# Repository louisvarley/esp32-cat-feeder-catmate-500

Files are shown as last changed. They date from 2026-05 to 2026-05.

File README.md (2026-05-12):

# ESP32 Cat Feeder (Cat Mate 500 + Home Assistant)

This project started for one simple reason: I needed to feed my cat properly when I was away. she only eats very small meals multiple times a day. 

The **Cat Mate C500** is great feeder, but it is built around a short timer cycle if only 24 hours. I wanted something I could control remotely and schedule flexibly with **Home Assistant**, including windows longer than 24 hours.

With two C500 units and ice packs, I can keep 8 small meals fresh for around **48 hours**. That gives me a much better safety margin for overnight trips and weekends for work. I prefer being able to watch on camera and judge when she needs feeding rather than 
merely a timer.

# ESP32-C3 Cat Feeder

A hacked C500 cat feeder controlled via a web interface and Home Assistant, built around an ESP32-C3 board with built-in OLED.

---

## Components

| Component | Value / Part | Purpose |
|---|---|---|
| ESP32-C3 with OLED | Diymore ESP32-C3 | Main controller, web server, display |
| IR Optical Sensor | ITR9608 | Detects bowl position, has one already but this is more reliable and is 3.3v compatable.. ok i might have blown up the originals... |
| NPN Transistor | 2N2222A | Motor switching |
| Flyback Diode | 1N4007 | Motor spike protection |
| Resistor | 1kΩ  | Transistor base current limiting |
| Resistor | 200Ω | IR LED current limiting |
| USB-C Breakout Board | With CC1/CC2 pins | Power input for mounting the power elsewhere |

---

## Wiring

### Power
```
USB 5V              →  V5 pin on ESP32
USB GND             →  GND pin on ESP32
CC1 on breakout     →  5.1kΩ  →  GND  (if not already on breakout board)
CC2 on breakout     →  5.1kΩ  →  GND  (if not already on breakout board)
```

### Motor Circuit
```
V3 (3.3V)           →  Motor +
Motor -             →  2N2222A Collector (middle leg, flat face forward)
2N2222A Emitter     →  GND              (left leg, flat face forward)
GPIO 3              →  1kΩ  →  2N2222A Base  (right leg, flat face forward)

Flyback diode across motor terminals:
  Stripe (cathode)  →  Motor + (3.3V side)
  No stripe (anode) →  Motor - (Collector side)
```

### IR Sensor (ITR9608)
```
Pin 1 (Anode)       →  200Ω  →  3.3V   (emitter/LED side)
Pin 2 (Cathode)     →  GND              (emitter/LED side)
Pin 3 (Collector)   →  GPIO 4           (receiver/output side)
Pin 4 (Emitter)     →  GND              (receiver/output side)
```

> Note: GPIO 4 uses INPUT_PULLUP in code — no external pull up resistor needed.

### OLED Display
```
Internal to board — no wiring needed
SDA  →  GPIO 5 (internal)
SCL  →  GPIO 6 (internal)
```

### Boot Button
```
Internal to board — no wiring needed
GPIO 9 (internal)
```

---

## GPIO Summary

| GPIO | Function |
|---|---|
| GPIO 3 | Motor control (via 2N2222A) |
| GPIO 4 | IR sensor signal |
| GPIO 5 | OLED SDA (internal) |
| GPIO 6 | OLED SCL (internal) |
| GPIO 9 | Boot button (internal) |

---

## Libraries Required

Install via Arduino IDE Library Manager:

- **U8g2** by oliver
- **WiFiManager** by tzapu

---

## Usage

### First Boot
1. Power on the device
2. Connect to the **CATFEEDER###** WiFi network (no password)
3. Open browser to **192.168.4.1**
4. Enter your WiFi details and select DHCP or Static IP
5. Device restarts and connects

### Web Interface
Navigate to the device IP address in any browser to access the feed button.

### Manual Feed
Press the boot button once to trigger a feed.

### Reset WiFi
Hold the boot button for 10 seconds — device clears WiFi settings and restarts into AP mode.

### Home Assistant
Add to `configuration.yaml`:
```yaml
rest_command:
  cat_feeder_1:
    url: "http://<device-ip>/feed"
    method: GET
```

Then call `rest_command.cat_feeder_1` from automations or the dashboard.

---

## Notes

- Motor runs on 3.3V — original feeder ran on 2-3x AA batteries so 3.3V is fine
- IR sensor requires 200Ω current limiting resistor on LED side — without it the LED will burn out
- WiFi TX power is reduced to `WIFI_POWER_8_5dBm` to fix cold boot connection issues on this board
- USB-C breakout board must have CC1 and CC2 pulled to GND via 5.1kΩ resistors to negotiate power from charger

## Libraries used

- `WiFi.h`
- `WebServer.h`
- `WiFiManager.h`
- `Preferences.h`
- `Wire.h`
- `U8g2lib.h`

Install these in Arduino IDE before compiling.

## Upload and run

1. Open `cat_feeder/cat_feeder.ino` in Arduino IDE.
2. Install required libraries.
3. Select your ESP32 board + COM port.
4. Upload firmware.
5. On first boot, connect to AP shown on OLED (`CATFEEDERxxx`) and set Wi-Fi.
6. Open the ESP32 IP address in browser or call `/feed` from Home Assistant.

## 3d Prints

Included 3 STL's for mounting the board in the space the existing LCD goes and for mounting external USB C breakout board with a little super glue! 

Enjoy! Spend time with your cat and don't let the robots do all the feeding!

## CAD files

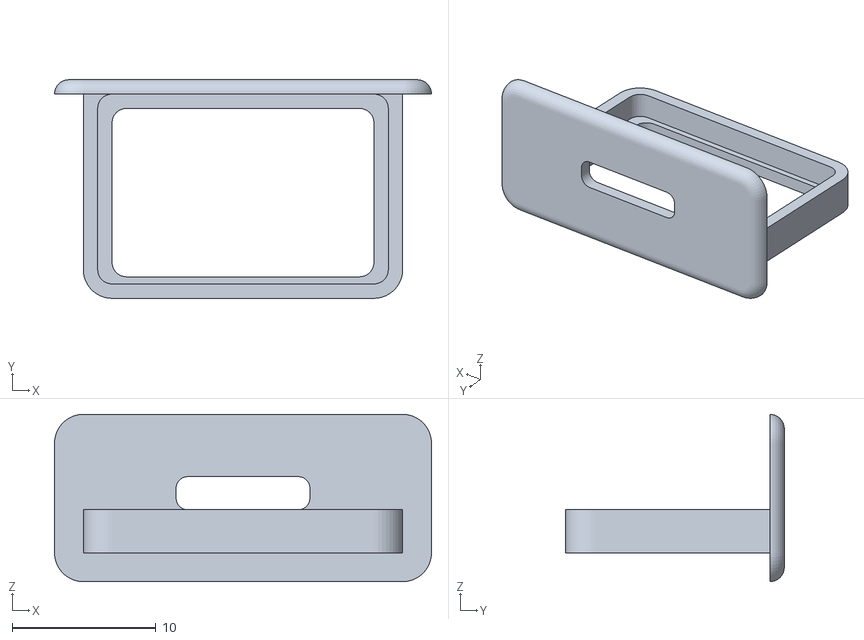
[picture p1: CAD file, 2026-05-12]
USB Socket.stl
26.2 x 15.2 x 11.6

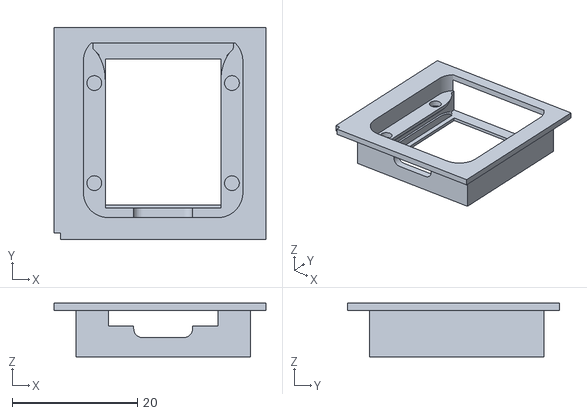
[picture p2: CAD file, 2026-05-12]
Holder.stl
33.9 x 33.9 x 8.62

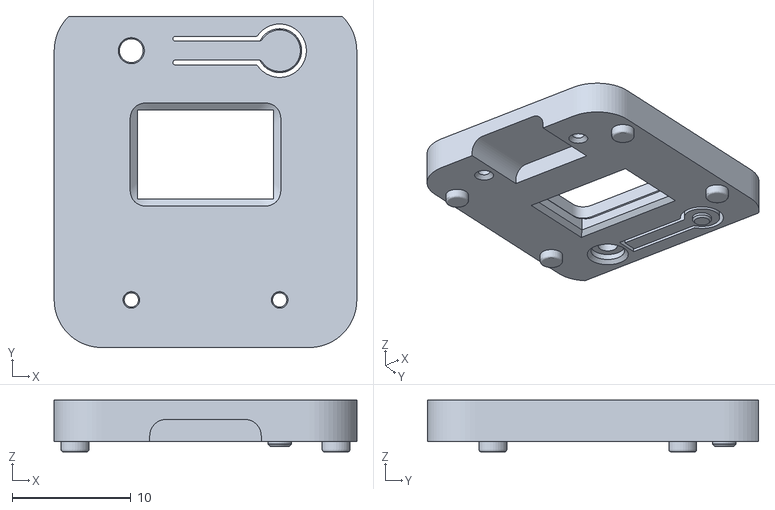
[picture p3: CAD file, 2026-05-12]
Cap.stl
25.5 x 27.9 x 4.38

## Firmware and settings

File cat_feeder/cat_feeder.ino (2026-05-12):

#include <WiFi.h>
#include <WebServer.h>
#include <WiFiManager.h>
#include <Preferences.h>
#include <Wire.h>
#include <U8g2lib.h>

#define MOTOR_PIN 3
#define SENSOR_PIN 4
#define BOOT_BUTTON 9
#define SDA_PIN 5
#define SCL_PIN 6

U8G2_SSD1306_72X40_ER_F_HW_I2C display(U8G2_R0, U8X8_PIN_NONE, SCL_PIN, SDA_PIN);
WebServer server(80);
Preferences preferences;

String lastFed = "Never";
bool feeding = false;

void updateOLED(String line1, String line2) {
  display.clearBuffer();
  display.setFont(u8g2_font_6x10_tr);
  display.drawStr(0, 12, line1.c_str());
  display.drawStr(0, 28, line2.c_str());
  display.sendBuffer();
}

void feed() {
  if (feeding) return;
  feeding = true;
  Serial.println("Feeding...");
  updateOLED("Feeding...", "");
  digitalWrite(MOTOR_PIN, HIGH);
  delay(200);
  unsigned long timeout = millis() + 5000;
  while (digitalRead(SENSOR_PIN) == HIGH) {
    if (millis() > timeout) {
      Serial.println("Timeout!");
      break;
    }
  }
  digitalWrite(MOTOR_PIN, LOW);
  lastFed = String(millis() / 60000) + "min ago";
  Serial.println("Fed!");
  updateOLED("Fed!", lastFed);
  delay(2000);
  feeding = false;
}

void handleRoot() {
  String html = "";
  html += "<!DOCTYPE html><html><head>";
  html += "<meta name='viewport' content='width=device-width, initial-scale=1'>";
  html += "<title>Cat Feeder</title>";
  html += "<style>";
  html += "body{font-family:sans-serif;display:flex;flex-direction:column;align-items:center;justify-content:center;min-height:100vh;margin:0;background:#1a1a2e;color:white;}";
  html += "h1{font-size:2em;margin-bottom:0.2em;}";
  html += "p{color:#aaa;margin-bottom:2em;}";
  html += "button{background:#e94560;color:white;border:none;padding:20px 50px;font-size:1.5em;border-radius:12px;cursor:pointer;}";
  html += "button:active{background:#c73652;}";
  html += ".last{margin-top:2em;color:#aaa;font-size:0.9em;}";
  html += "</style></head><body>";
  html += "<h1>Cat Feeder</h1>";
  html += "<p>Press to dispense one portion</p>";
  html += "<button onclick=\"fetch('/feed').then(function(){document.querySelector('.last').innerText='Feeding...';setTimeout(function(){location.reload();},3000);})\">Feed Now</button>";
  html += "<div class='last'>Last fed: " + lastFed + "</div>";
  html += "</body></html>";
  server.send(200, "text/html", html);
}

void handleFeed() {
  feed();
  server.send(200, "text/plain", "OK");
}

void setup() {
  Serial.begin(115200);
  delay(6000);  // wait for everything to stabilise on cold boot

  pinMode(MOTOR_PIN, OUTPUT);
  pinMode(SENSOR_PIN, INPUT_PULLUP);
  pinMode(BOOT_BUTTON, INPUT_PULLUP);
  digitalWrite(MOTOR_PIN, LOW);

  Wire.begin(SDA_PIN, SCL_PIN);
  display.begin();
  updateOLED("Starting...", "");

  // Generate random AP name
  String apSSID = "CATFEEDER" + String(random(100, 999));

  WiFiManager wm;

  // Show AP info on OLED when in config mode
  wm.setAPCallback([apSSID](WiFiManager* wm) {
    updateOLED("AP Mode", apSSID);
  });

  updateOLED("WiFi...", "Connecting...");
  WiFi.mode(WIFI_STA);
  WiFi.setTxPower(WIFI_POWER_8_5dBm);

  // autoConnect blocks until connected
  // if no saved credentials, opens AP with given name
  if (!wm.autoConnect(apSSID.c_str())) {
    updateOLED("WiFi Failed!", "Restarting...");
    delay(3000);
    ESP.restart();
  }

  String ip = WiFi.localIP().toString();
  Serial.println("Connected! IP: " + ip);
  updateOLED("Ready!", ip);

  server.on("/", handleRoot);
  server.on("/feed", handleFeed);
  server.begin();
}

void loop() {
  server.handleClient();
  yield();

  // Rotate OLED between IP and last fed
  static unsigned long lastOLEDSwitch = 0;
  static bool showIP = true;
  if (!feeding && millis() - lastOLEDSwitch > 5000) {
    lastOLEDSwitch = millis();
    if (showIP) {
      updateOLED("IP:", WiFi.localIP().toString());
    } else {
      updateOLED("Last fed:", lastFed);
    }
    showIP = !showIP;
  }

  // Boot button
  if (digitalRead(BOOT_BUTTON) == LOW) {
    unsigned long pressStart = millis();
    while (digitalRead(BOOT_BUTTON) == LOW) {
      delay(10);
      if (millis() - pressStart >= 10000) {
        updateOLED("Resetting", "WiFi...");
        delay(1000);
        WiFiManager wm;
        wm.resetSettings();
        ESP.restart();
      }
    }
    if (millis() - pressStart < 10000) {
      feed();
    }
  }
}
